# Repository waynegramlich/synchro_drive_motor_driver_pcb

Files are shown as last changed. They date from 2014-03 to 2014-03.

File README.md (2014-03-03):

# synchro_drive_motor_driver_pcb

This printed circuit board drives two brushed DC motors for a
synchro drive.   A synchro drive allows a single wheel to
be driven and turned independently without any wheel skidding.

## Revision A

This board is designed around U1 and U2, a couple of AS5050
hall effect 10-bit absolute rotation sensors.  The board is
arrange to place both of these sensors exactly over the
magnets on top of the twist motor and drive motor shafts.

The board geometry is constrained by synchro drive motor
assembly.  The motor pulleys are fully enclosed to keep
dirt and grime from gumming up the pulleys.  Thus, the
PCB has an enclosed section on the bottom and an
exposed section on the top.  The exposed section is where
all of the heat generating electronics is placed to provide
additional air flow to remove excess heat.

The electronics is divided into two electrically isolated
sections:

* The processor section is connected to the Logic power/ground
  and can communicate over the CAN bus.

* The motor section is connected to the Motor power/ground
  and drives the motor H-bridges.

### Processor Section

The power and communication comes in on the 26-pin N1 connector.

The motor power (MPWR) and motor ground (MGND) are routed to
the motor section (see below.)

The logic power (LPWR) and logic ground (LGND) are sent through
C1, U3, C3, U6, C9, and C11 to provide regulated 5 volts and 3.3
volts.  The LM2931 (U3) is must be able to take up to 30 volts
input.  This requires a DPAK package to provide adequate heat
dissipation.  C3 must be a tantalum capacitor to get an ESR
(Equivalent Series Resistance) less than 400mOhm.

There are two signals (SEL_LR and SEL_FB) that can be
testing in software to specify whether the wheel is left/right
or front/back.

The communication comes in over CANH and CANL and is run into
an MCP2562 (U4) CAN bus transceiver.  The MCP2562 is the only
part that must run at 5 volts.  By setting the VIO input (pin 5)
to 3.3V the processor can directly communicate with the transceiver
using 3.3V signaling.

The processor is TM4C123GH6PM, an Arm Cortex M4-F class
microcontroller.  The processor is run using a 10MHz crystal
X1 and two 18pF capactiors C10 and C11.  There is a reset
button (SW1) with a 10K pull-up resistor (R2).

The AS5050 hall effect rotation sensors (U1 and U2) are each
tied to a dedicated SPI intefaces (SSI0 and SSI1, repsectively.)

For debugging, there is 6-pin connector (N2) that is designed
to connect to FTDI 3.3V USB to serial cable.  The LED (D1) and
current limiting resistor (R1) are also available for debugging.
Jumper J1 is meant to implement physical signal that allows\
over the bus firmware updating to be enabled or disabled.  J1
is also available for debugging.

The processor can be programmed and debugged via either of the
JTAG/SWDEBUG connectors (N3 or N4).  Both connectors conform to
the ARM 10-pin JTAG/SWDEBUG connector specification.  One connector
is .05inch pitch and the other is .10inch pitch.

The motor directions are specified by PB0-3 (pins 45-48).
Third SPI peripheral (SSI3) is dedicated to controlling the DAC
(Digital to Analog Converter) in the motor section.

There are the usual bypass capacitors (C2-C8, C22-23)
and mounting holes (H1-H4, H6-H9).  There are two additional
holes (H5, H10) that are aligned with the motor drive shafts.

### Motor section

Motor power is passed through C13, U7, and U14 to provide
regulated 5V for the various integrated circuits.  There is
no 3.3V in this section.

The H-bridges are venerable bipolar L298's (U13, U14) with
8 Schottky current shunt diodes.  The L298's are dual H-bridges
that have been ganged together to provide 3A of continuous
current.  The motors are connected to N5 and N6.

The direction control signals change infrequently, so they
are directed through inexpensive (and lower bandwidth)
optoisolator chips (U10, U11) with current limit resistors
(R3-R6).  Resistors R7-R10 are pull-up resistors that are
fed into IN1-IN4 inputs of the H-bridge chips.

The DAC is controlled with SPI signaling through the SI8420
chips.  This are electrically isolated chips that can send
digital signals at up to 1MHz.  The SEL, SCK and SDI signals
are sent through these chip to the DAC chip (U15).

The DAC chip is an MCP48?2, which a dual channel DAC.
The output of each DAC is used to set the maximum voltage
across the H-bridge current sense resistors (R11, R12).
The DAC outputs are compared to the sense resistor voltages
using the MCP6542 comparator chip (U16).  Whenever the
current through the sense resistor exceeds the DAC output
voltage, the enable pins for the L298 are cleared through
the dual D flip-flops (U12).

The way this works, is that the processor sends out a
25KHz square wave through U9 (pin 2).  This signal clocks
a 1 into both flip-flops, thereby enabling both H-bridges.
As the current builds up across the current sense resistor,
the flip-flops are cleared to disable the H-bridge enable
pin.  This results in a PWM (pulse width modulated) signal
on the H-bridge enable pin, where the electronics ensures
that the maximum amount of current specified by the DAC
voltage is not exceeded.

There are the usual set of bypass capacitors (C15-C21)
and test points for debugging.

### Rev. A Notes

* The current sense resistor is too big.  At maximum
  current (3A), the resistor will generate 5W of power.
  The current sense resistors are only 2W devices.
  The resistor needs to be dropped from .56 Ohm to
  .2 Ohm.  This will require changing the DAC to
  be one that has a maximum voltage input rather
  than an internally generated one.

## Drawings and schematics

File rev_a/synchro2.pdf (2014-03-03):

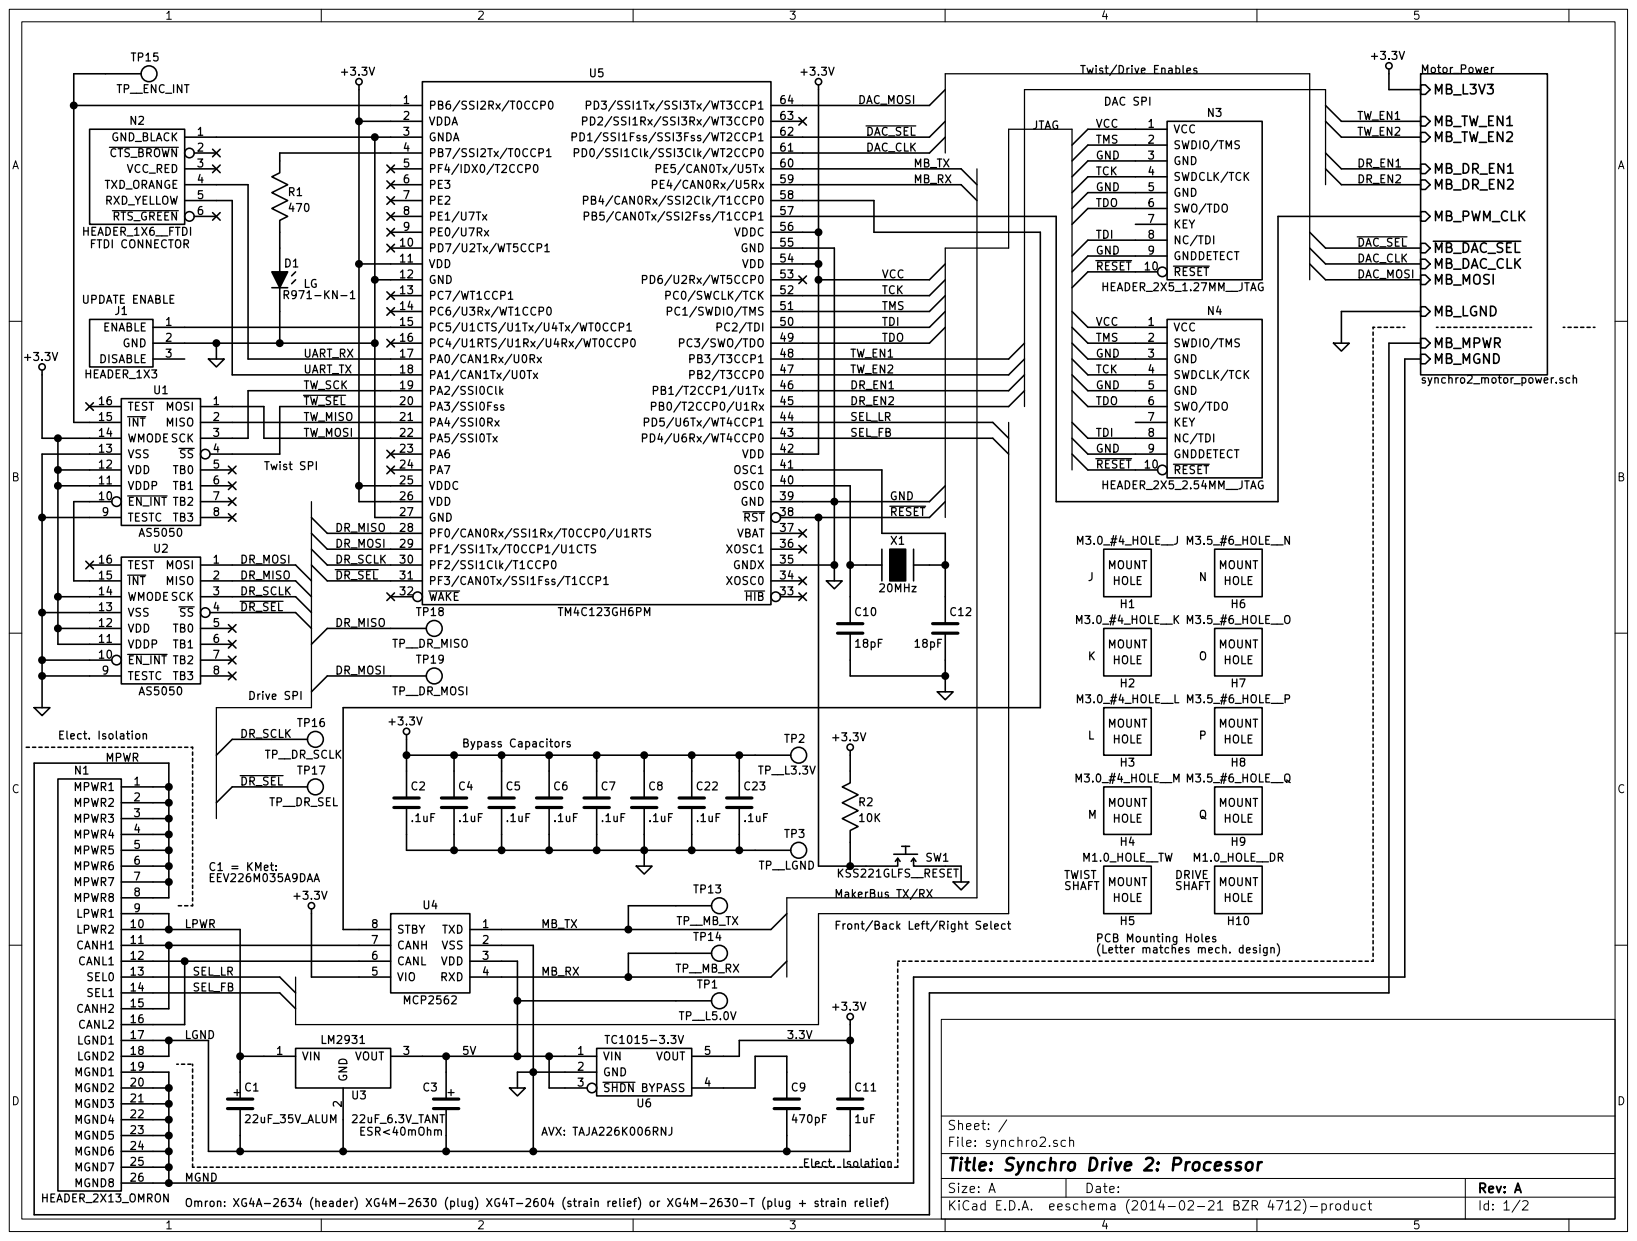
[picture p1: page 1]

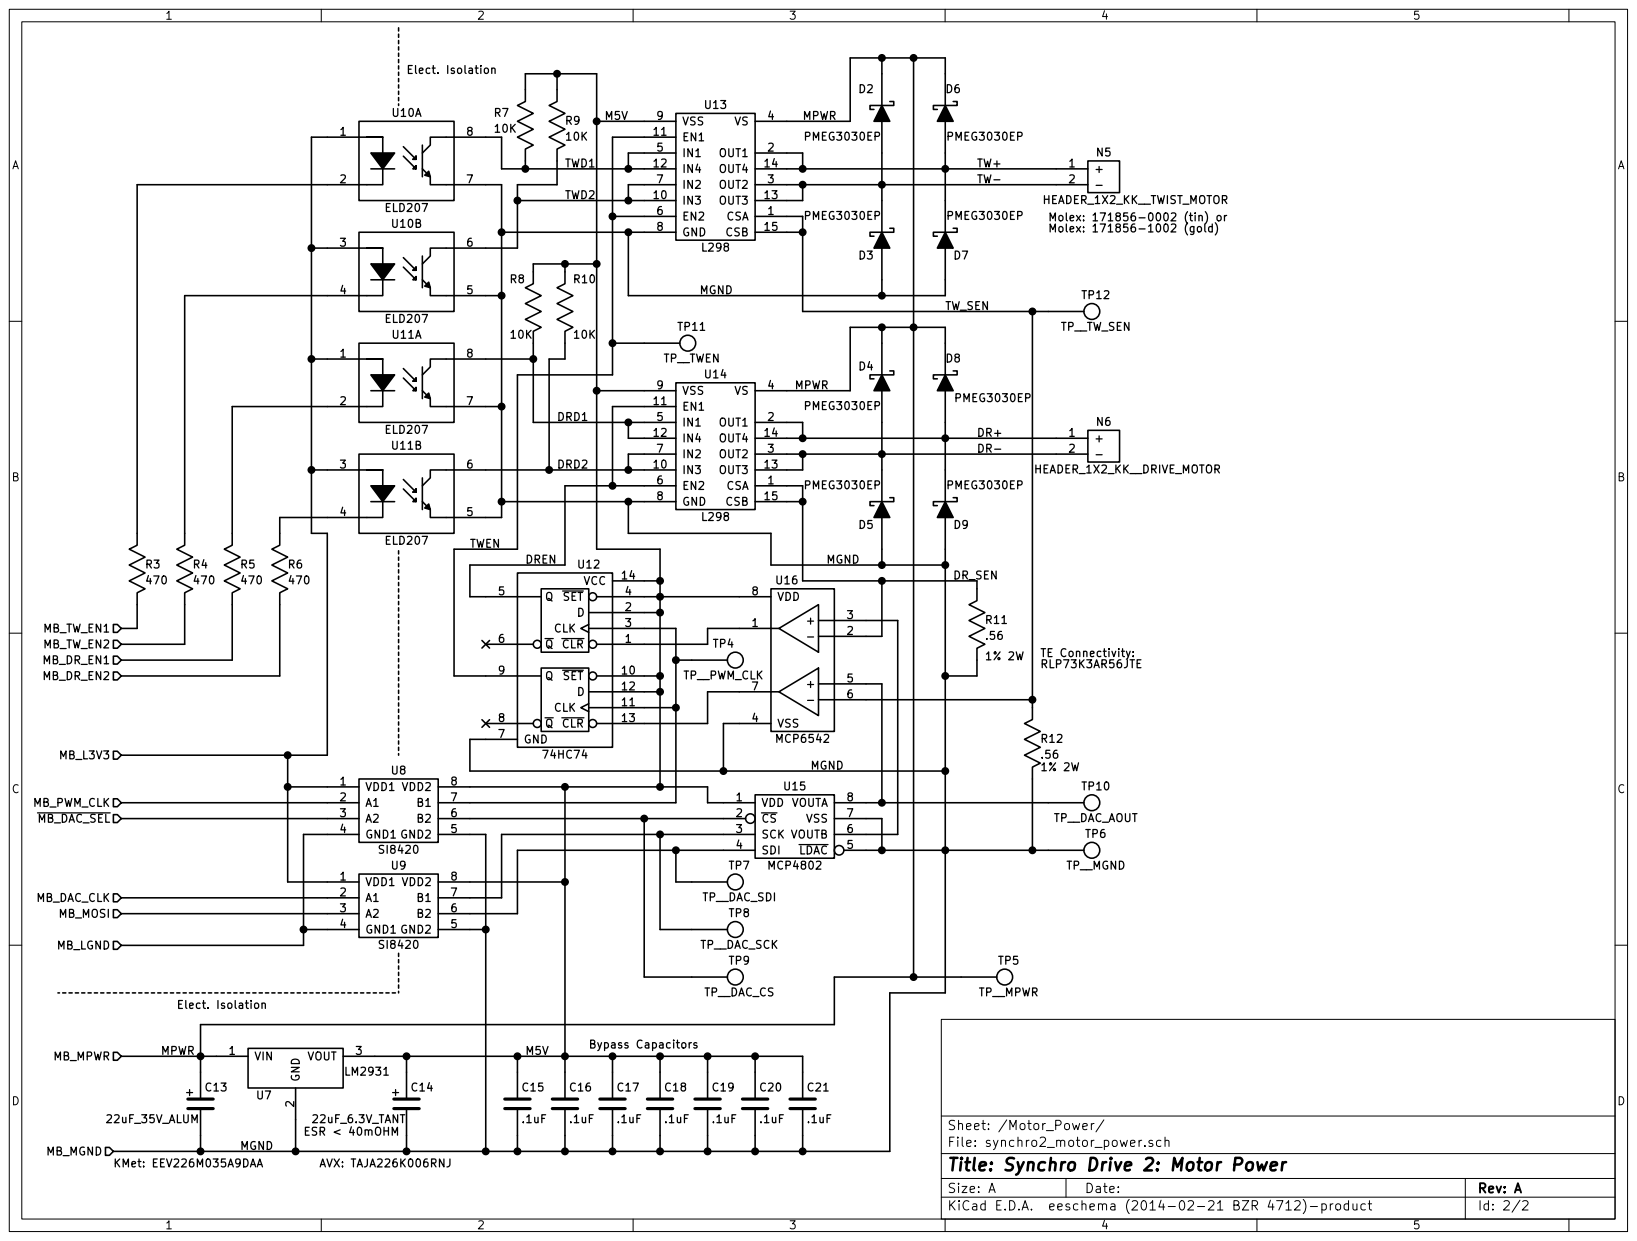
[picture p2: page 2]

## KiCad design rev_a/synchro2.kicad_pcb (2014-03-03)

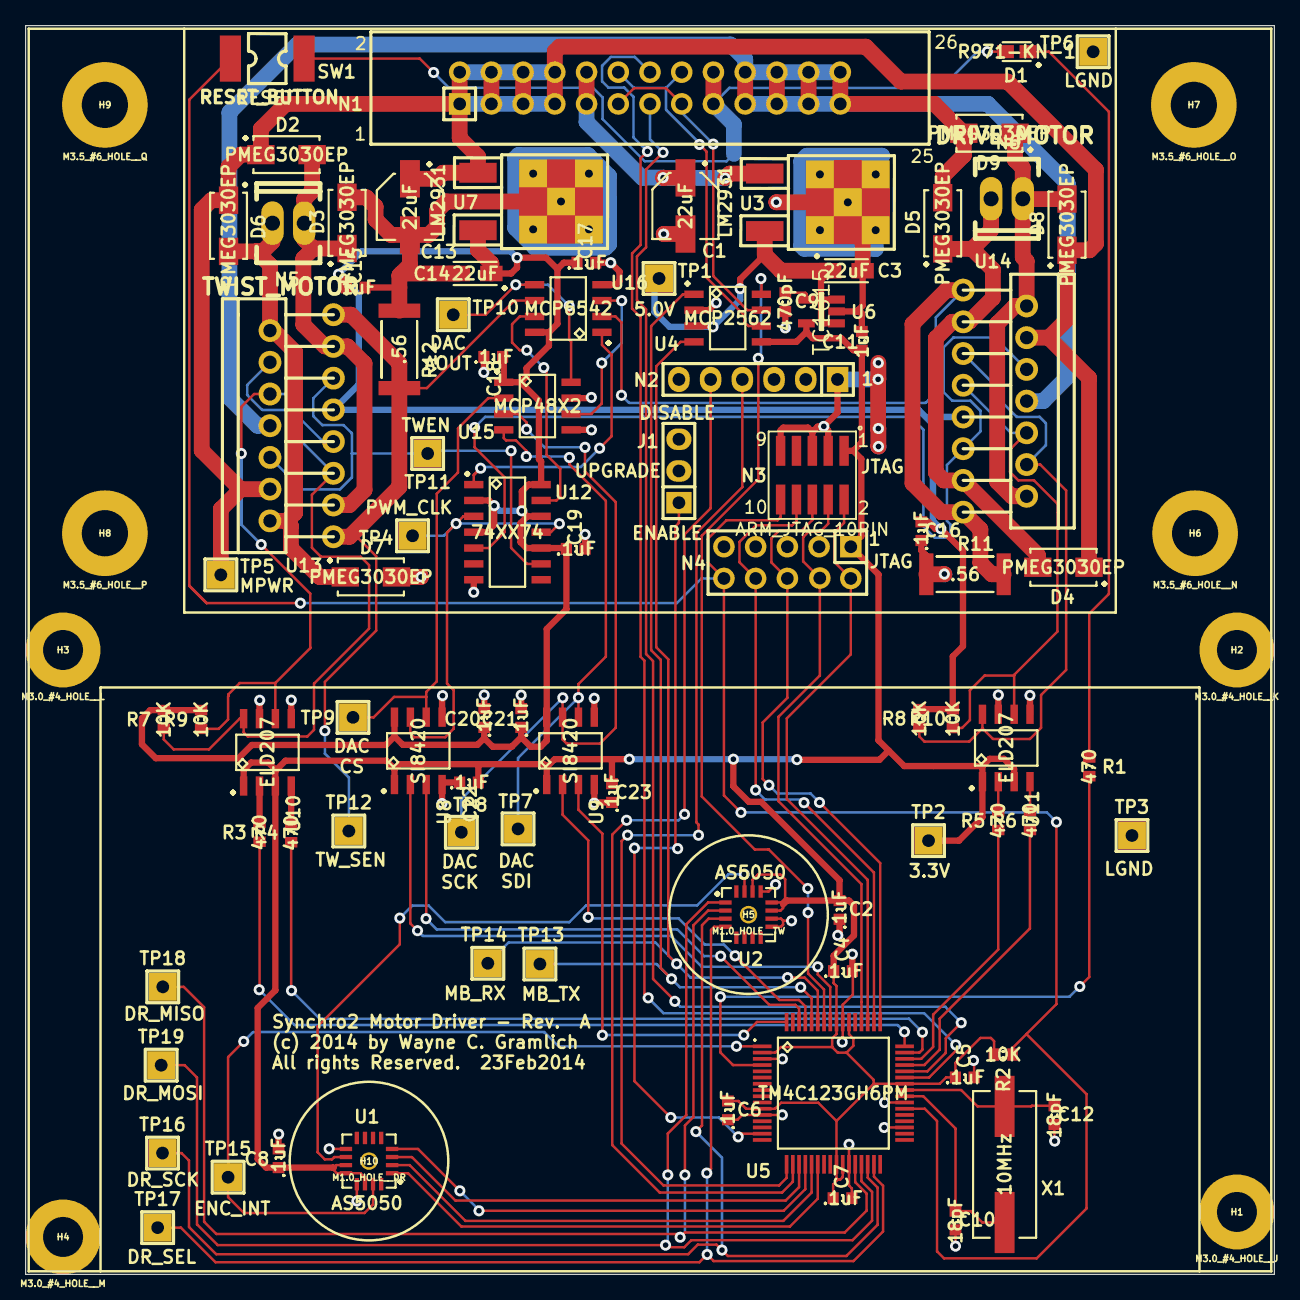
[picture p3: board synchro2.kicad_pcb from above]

Board: 2 copper layers, 100.0 x 100.0 mm, 98 parts (0 on the bottom side), 69 nets.

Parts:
C1, C13: 22uF; CAPAE530X540N
C2, C4, C5, C6, C7, C8, C15, C16, C17, C18, C19, C20, C21, C22, C23: .1uF; CAPC1608X55N
C3, C14: 22uF; CAPMP3216X180N
C9: 470pF; CAPC1608X55N
C10, C12: 18pF; CAPC1608X55N
C11: 1uF; CAPC1608X55N
D1: R971-KN-1; DIOM2012X160N
D2, D3, D4, D5, D6, D7, D8, D9: PMEG3030EP; DIOM5027X244N
H1: M3.0_#4_HOLE__J; M3.0_#4_HOLE
H2: M3.0_#4_HOLE__K; M3.0_#4_HOLE
H3: M3.0_#4_HOLE__L; M3.0_#4_HOLE
H4: M3.0_#4_HOLE__M; M3.0_#4_HOLE
H5: M1.0_HOLE__TW; M1.0_HOLE
H6: M3.5_#6_HOLE__N; M3.5_#6_HOLE
H7: M3.5_#6_HOLE__O; M3.5_#6_HOLE
H8: M3.5_#6_HOLE__P; M3.5_#6_HOLE
H9: M3.5_#6_HOLE__Q; M3.5_#6_HOLE
H10: M1.0_HOLE__DR; M1.0_HOLE
J1: UPDATE_ENABLE; Pin_Header_Straight_1x03
N1: OMRON XG4A-2632; OMRON_X4GA_2632
N2: FTDI_CONN; Pin_Header_Straight_1x06
N3: ARM_JTAG_10PIN; SMT_VERT_M1.27_2x5
N4: ARM_JTAG_10PIN; ARM_JTAG_2X5_2.54MM
N5: TWIST_MOTOR; Socket_MOLEX-KK-RM2-54mm_Lock_2pin_straight
N6: DRIVE_MOTOR; Socket_MOLEX-KK-RM2-54mm_Lock_2pin_straight
R1, R3, R4, R5, R6: 470; RESC1608X50N
R2, R7, R8, R9, R10: 10K; RESC1608X50N
R11, R12: .56; RESC6432X76N
SW1: RESET_BUTTON; KSS221GLFS
TP1: L5.0V; TEST_POINT
TP2: L3.3V; TEST_POINT
TP3: LGND; TEST_POINT
TP4: PWM_CLK; TEST_POINT
TP5: MPWR; TEST_POINT
TP6: MGND; TEST_POINT
TP7: DAC_SDI; TEST_POINT
TP8: DAC_SCK; TEST_POINT
TP9: DAC_CS; TEST_POINT
TP10: DAC_AOUT; TEST_POINT
TP11: TWEN; TEST_POINT
TP12: TW_SEN; TEST_POINT
TP13: MB_TX; TEST_POINT
TP14: MB_RX; TEST_POINT
TP15: ENC_INT; TEST_POINT
TP16: DR_SCLK; TEST_POINT
TP17: DR_SEL; TEST_POINT
TP18: DR_MISO; TEST_POINT
TP19: DR_MOSI; TEST_POINT
U1, U2: AS5050; QFN65P400X400X80-16N
U3, U7: LM2931; DPAK_THERMAL
U4: MCP2562; SOIC127P600X175-8N
U5: TM4C123GH6PM; QFP50P1200X1200X145-64N
U6: TC1015; SOT95P280X145-5N
U8, U9: SI8420; SOIC127P600X175-8N
U10, U11: ELD207; SOIC127P600X175-8N
U12: 74XX74; SOIC127P600X175-14N
U13, U14: L298; MULTIWATT15
U15: MCP48X2; SOIC127P600X175-8N
U16: MCP6542; SOIC127P600X175-8N
X1: 10MHz; XTAL1150X480X430N

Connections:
3.3V: C2.1, C4.1, C5.1, C6.1, C7.1, C8.1, C11.1, C22.1, C23.1, N3.1, N4.1, R2.2, TP2.1, U1.11, U1.12, U1.14, U2.11, U2.12, U2.14, U4.5, U5.2, U5.11, U5.25, U5.26, U5.42, U5.54, U5.56, U6.5, U8.1, U9.1, U10.1, U10.3, U11.1, U11.3
/5V: C3.1, TP1.1, U3.3, U4.3, U6.1, U6.3
/DR_MISO: TP18.1, U2.2, U5.28
/DR_MOSI: TP19.1, U2.1, U5.29
/DR_SCLK: TP16.1, U2.3, U5.30
/LPWR: C1.1, N1.9, N1.10, U3.1
/MB_RX: TP14.1, U4.4, U5.59
/MB_TX: TP13.1, U4.1, U5.60
/Motor_Power/DR+: D8.2, D9.1, N6.1, U14.2, U14.14
/Motor_Power/DR-: D4.2, D5.1, N6.2, U14.3, U14.13
/Motor_Power/DRD1: R8.1, U11.8, U14.5, U14.12
/Motor_Power/DRD2: R10.1, U11.6, U14.7, U14.10
/Motor_Power/DREN: U12.5, U14.6, U14.11
/Motor_Power/DR_SEN: R11.2, U14.1, U14.15, U16.2
/Motor_Power/M5V: C14.1, C15.1, C16.1, C17.1, C18.1, C19.1, C20.1, C21.1, R7.2, R8.2, R9.2, R10.2, U7.3, U8.8, U9.8, U12.2, U12.4, U12.10, U12.12, U12.14, U13.9, U14.9, U15.1, U16.8
/Motor_Power/MB_DAC_CLK: U5.61, U9.2
/Motor_Power/MB_DR_EN1: R5.1, U5.46
/Motor_Power/MB_DR_EN2: R6.1, U5.45
/Motor_Power/MB_MGND: C13.2, C14.2, C15.2, C16.2, C17.2, C18.2, C19.2, C20.2, C21.2, D3.2, D5.2, D7.2, D9.2, N1.19, N1.20, N1.21, N1.22, N1.23, N1.24, N1.25, N1.26, R11.1, R12.1, TP6.1, U7.2, U8.5, U9.5, U10.5, U10.7, U11.5, U11.7, U12.7, U13.8, U14.8, U15.5, U15.7, U16.4
/Motor_Power/MB_MOSI: U5.64, U9.3
/Motor_Power/MB_MPWR: C13.1, D2.1, D4.1, D6.1, D8.1, N1.1, N1.2, N1.3, N1.4, N1.5, N1.6, N1.7, N1.8, TP5.1, U7.1, U13.4, U14.4
/Motor_Power/MB_PWM_CLK: U5.57, U8.2
/Motor_Power/MB_TW_EN1: R3.1, U5.48
/Motor_Power/MB_TW_EN2: R4.1, U5.47
/Motor_Power/TW+: D6.2, D7.1, N5.1, U13.2, U13.14
/Motor_Power/TW-: D2.2, D3.1, N5.2, U13.3, U13.13
/Motor_Power/TWD1: R7.1, U10.8, U13.5, U13.12
/Motor_Power/TWD2: R9.1, U10.6, U13.7, U13.10
/Motor_Power/TWEN: TP11.1, U12.9, U13.6, U13.11
/Motor_Power/TW_SEN: R12.2, TP12.1, U13.1, U13.15, U16.6
/Motor_Power/~MB_DAC_SEL: U5.62, U8.3
/SEL_FB: N1.14, U5.43
/SEL_LR: N1.13, U5.44
/TCK: N3.4, N4.4, U5.52
/TDI: N3.8, N4.8, U5.50
/TDO: N3.6, N4.6, U5.49
/TMS: N3.2, N4.2, U5.51
/TW_MISO: U1.2, U5.21
/TW_MOSI: U1.1, U5.22
/TW_SCK: U1.3, U5.19
/UART_RX: N2.4, U5.17
/UART_TX: N2.5, U5.18
/~DR_SEL: TP17.1, U2.4, U5.31
/~RESET: N3.10, N4.10, R2.1, SW1.1, U5.38
/~TW_SEL: U1.4, U5.20
GND: C1.2, C2.2, C3.2, C4.2, C5.2, C6.2, C7.2, C8.2, C9.2, C10.2, C11.2, C12.2, C22.2, C23.2, D1.2, J1.2, N1.17, N1.18, N2.1, N3.3, N3.5, N3.9, N4.3, N4.5, N4.9, SW1.2, TP3.1, U1.9, U1.13, U2.9, U2.10, U2.13, U3.2, U4.2, U5.3, U5.12, U5.27, U5.35, U5.39, U5.55, U6.2, U8.4, U9.4
unnamed: C9.1, U6.4
unnamed: C10.1, U5.40, X1.1
unnamed: C12.1, U5.41, X1.2
unnamed: D1.1, R1.1
unnamed: J1.1, U5.15
unnamed: N1.11, N1.15, U4.7
unnamed: N1.12, N1.16, U4.6
unnamed: R1.2, U5.4
unnamed: R3.2, U10.2
unnamed: R4.2, U10.4
unnamed: R5.2, U11.2
unnamed: R6.2, U11.4
unnamed: TP4.1, U8.7, U12.3, U12.11
unnamed: TP7.1, U9.6, U15.4
unnamed: TP8.1, U9.7, U15.3
unnamed: TP9.1, U8.6, U15.2
unnamed: TP10.1, U15.8, U16.5
unnamed: TP15.1, U1.15, U5.1
unnamed: U1.10, U2.15
unnamed: U4.8, U5.58
unnamed: U12.1, U16.1
unnamed: U12.13, U16.7
unnamed: U15.6, U16.3

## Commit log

2014-02-01 Basic schematic is done.
    [synchro2.sch, synchro2_motor_power.sch]
2014-02-25 Rev. A is pretty close to being ready.
    [synchro2.kicad_pcb, synchro2.sch, synchro2_motor_power.sch]
2014-02-25 Almost done with Rev. A.
    [synchro2.kicad_pcb]
2014-02-26 Rev. A is ready.
    [synchro2-B_Cu.gbl, synchro2-B_Mask.gbs, synchro2-B_SilkS.gbo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]
2014-03-03 Tweak compennt values to match pricing database. No footprints were changed.
    [synchro2-B_Cu.gbl, synchro2-B_Mask.gbs, synchro2-B_SilkS.gbo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]

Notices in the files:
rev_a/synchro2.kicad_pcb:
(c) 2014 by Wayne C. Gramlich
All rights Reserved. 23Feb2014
